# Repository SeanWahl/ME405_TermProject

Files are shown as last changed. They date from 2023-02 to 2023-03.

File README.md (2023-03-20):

# ME 405 Term Project: Nerf Sentry Turret

Group: Mecha15
Sean Wahl, Nathan Dodd, Lewis Kanagy

## Overview

The goal of the Nerf Sentry Turret project is to learn by doing some of the most importnat topics in ME 405. These topics include 
designing systems of modest complexity with both mechanical and electrical components, using control systems to operate mechanical systems, and 
organizing software into discrete modules to call between python files. 

The project entails the consturction and calibration of a thermal sensing target acquisition system that can launch a projectile beyond 
16 feet. The team must use a given thermal camera, STM32 MCU Unit, and a selected Nerf launcher to "duel" an opposing team. The two teams are 
placed 16 feet apart, and upon a "Start" signal, the opposing systems must rotate 180 degrees using mechanical components, gather thermal data through I2C communication,
and use electical components to fire the launcher.

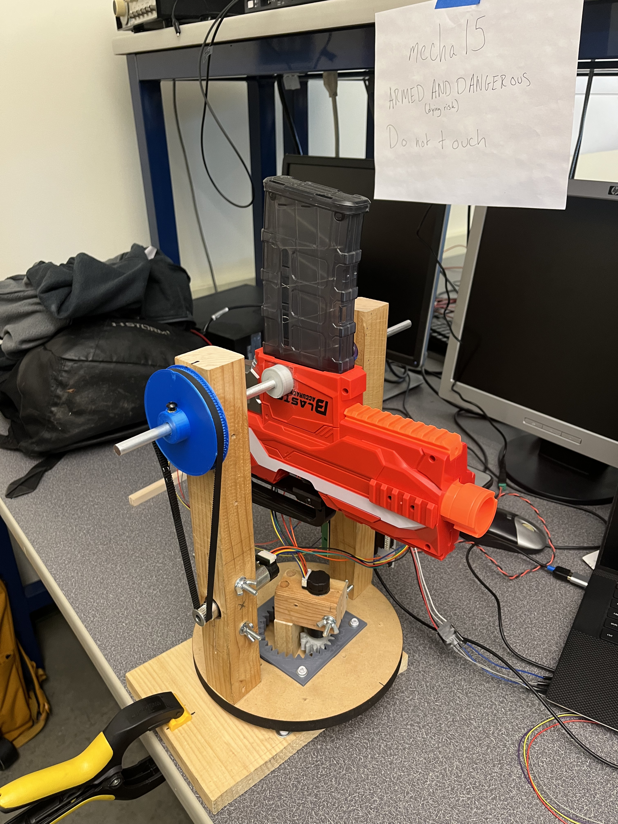
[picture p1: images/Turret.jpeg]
Final Turret


Figure 5.1. Final Nerf Sentry Turret Design

## Mechanical Design

The group began by mechanically designing the spinning base of the system, as seen in Figure 5.2. The system consists of a 3-D printed Internal gear, rotated by another
3-D printed gear head press fit onto the given ME 405 motor shaft. The circular wooden base rotates upon the rectangular base via a purchased, commercially available 
"lazy susan." The motor is mounted using a similar system to the ME 405 motor mounts, with a through hole in a wooden block tightened to hold the motor from the compressive
force applied thorugh the screw/wingnut components. Therefore, as the motor is spun, it rotates the entire circular wooden base which all components rest upon. 

Base Assembly

FIgure 5.2. Base Assembly

The top assembly was constructed the following week, composing of two standing obelisks, two bearings, the mounted shaft, and finally, the nerf gun. The obelisks are screwed
into the circular base, and with one of the obelisks using a similar clamping mechanism as the "yaw" motor to mount the "pitch" motor. The rotating mechanism is controlled by 
the gear-pulley system seen in Figure 5.1. Additionally, through holes are drilled  in the top of each obelisk to allow the alumnium shaft to pass thorugh, with bearings inlayed 
in the wood to house the metal shaft. Finally, the nerf gun is mounted to the shaft via 3-D printed brackets press fit onto the shaft; these brackets have a flat portion, as does the 
shaft, allowing the rotating shaft to rotate the gun as needed.

## Electrical Design

Mounted to the bottom assembly is the given ME 405 STM32 MCU unit, including the proper motor driver board (Figure 5.3). The MCU has wiring to the base motor (yaw) and obelisk 
motor (pitch) to give the system its two degrees of freedom; the intitialization, operation, and control of these motors can be found in the attached source code. The 
nerf gun itself is operated through a "hotwiring" approach, with the its two systems, flywheel and dart push mechanisms, wired to an attached bread board. The board 
contains relays, resistors, and mosfets to apply a set amount of voltage to the gun from the Nucleo GPIO pins. 

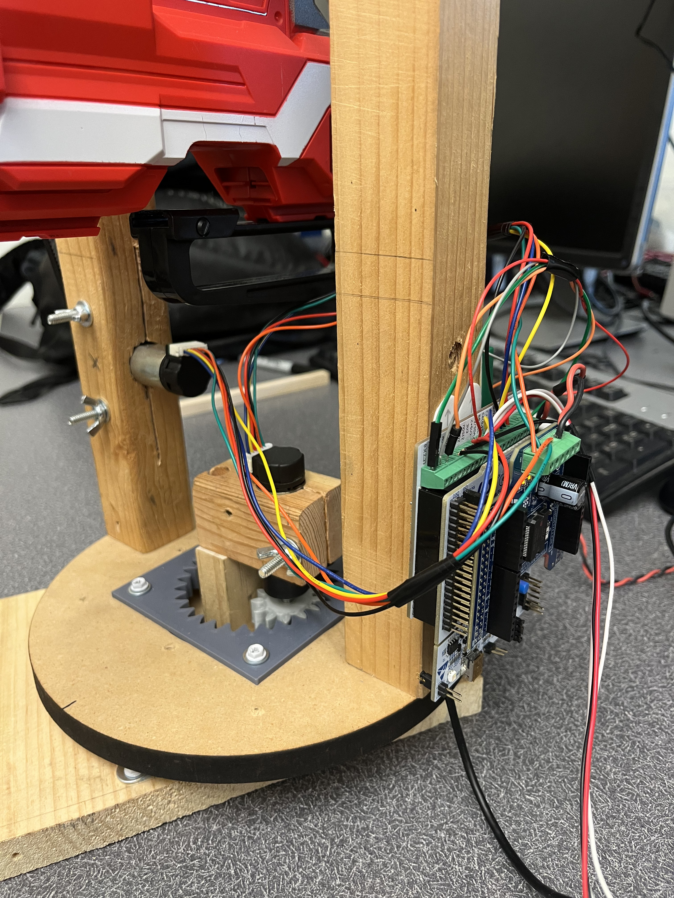
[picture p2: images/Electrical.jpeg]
Electronics


Figure 5.3. Electrical Assembly

## Software Design 

The software used for the project can all be found in the source code folder (src) found in the github page. A general overview of the software design can be better understood by 
looking at the attached State Transition Diagrams found at the bottom of the README file. 

Touching upon the thermal camera tracking algorithim, the camera was placed 8 feet in front of the turret system in order to give the highest image resolution to be analyzed. Within the 
mlx_camera.py file, the data received through the lens was a 24 row x 32 column csv grid of values 0-99, representing the magnitude of heat signature received. The code added to
the given mlx_camera.py analyzed each column upon taking a photo, averaged values in each column, and returned the column index. Given that opponents could only stand up against the table
and not off the sides, the table width was mapped out to the number of columns the camera can place. Assuming that the camera and turret would be placed in the same location every test, 
a unit conversion between (table width/columns) and (yaw position/table width) allowed a set position to be sent to the motor for a given "hottest column." A rough sketch of this can be
found below in Figure 5.4.

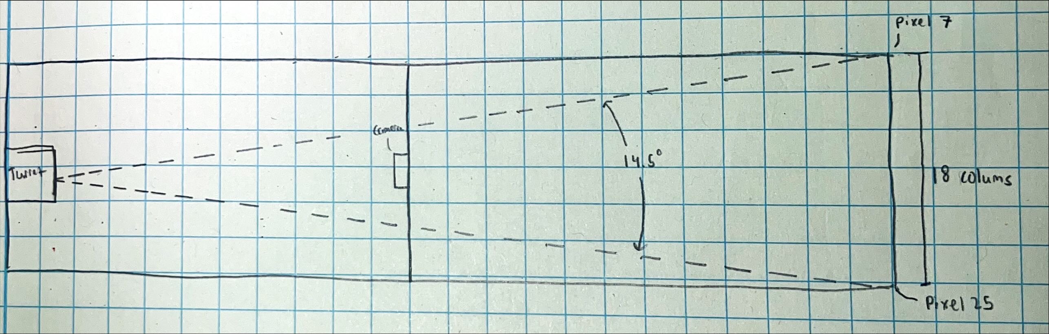
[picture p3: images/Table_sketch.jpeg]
Table Sketch


Figure 5.4. Sketch of table geometry to derive yaw motor setpoint given a "hot column" value.

## Project Results

The system that was designed, manufactured, and tested performed exceedingly well in testing prior to the performance on the dueling day. In nearly every test ran in which the motors
were set to a given setpoint, the thermal camera was allowed 1 second to record a picture, and the opponent did not move within the 1 second, the sentry could accurately move the yaw
motor and "track" a given heat signature and fire at will. When facing opponents in the testing phase, the turret would hit the opponent first before the opponent would fire, 
allowing the team to gain confidence heading into the dueling day. Come match day, all mechanical and electrical components worked, however in the final critical round, the 
magazine was forgotten to be refilled, leading to a defeat. Although this was difficult to grasp, the team was confident that should the magazine have been loaded, it surely would have
resulted in a hit target and a victory.

After undertaking this project for 3 weeks, the team has learned an outstanding amount about the mechatronics design process; even more so, the group has learned what worked well
and what has not for our specific system. Regarding software design, we originally attempted to configure the cotask.py, task_share.py, and basic_tasks.py files to allow for 
priority based scheduling of tasks. We quickly encountered problems, as this priorty task organization encountered issues when tasks, such as the camera task needing over 1 second
to capture an image, would go over its set period time. Instead, the software design of the main file entailed a much simpler finite state machine, swithcing between two simple states.
Going away from this task-sharing system sooner rather than later would have allowed for more time for the group to finalize designs such as camera placement, 

What worked well mechanically was the relatively small gear ratio for the "yaw" axis. The base plate was able to turn around quickly compared to other groups in the section, primarily
due to the gear ratio of 2.5. When facing groups with many more teeth on their internal gears, they were mechanically limited in the speed at which they could rotate. 
3-D printing the gears allowed for larger design control over this element; larger gear teeth worked well, as they were easier to mesh than the much smaller, 16 teeth gears supplied
in class.

Should further testing and design take place on this specific assembly, a useful addition would be a concrete electrical wiring setup. Given the team was still conducting basic testing
upon the dueling date, a clear, robust wiring setup could not be formed. Further research could also be done to use a different MCU running C/C++ code, as this seemed succesful for 
other groups in allowing for up to 60 captures / second; the software/hardware used permitted for roughly 1 capture/second. Further research could prove a useful project for one
interested in any robotics, mechanical design, or thermal camera applications.

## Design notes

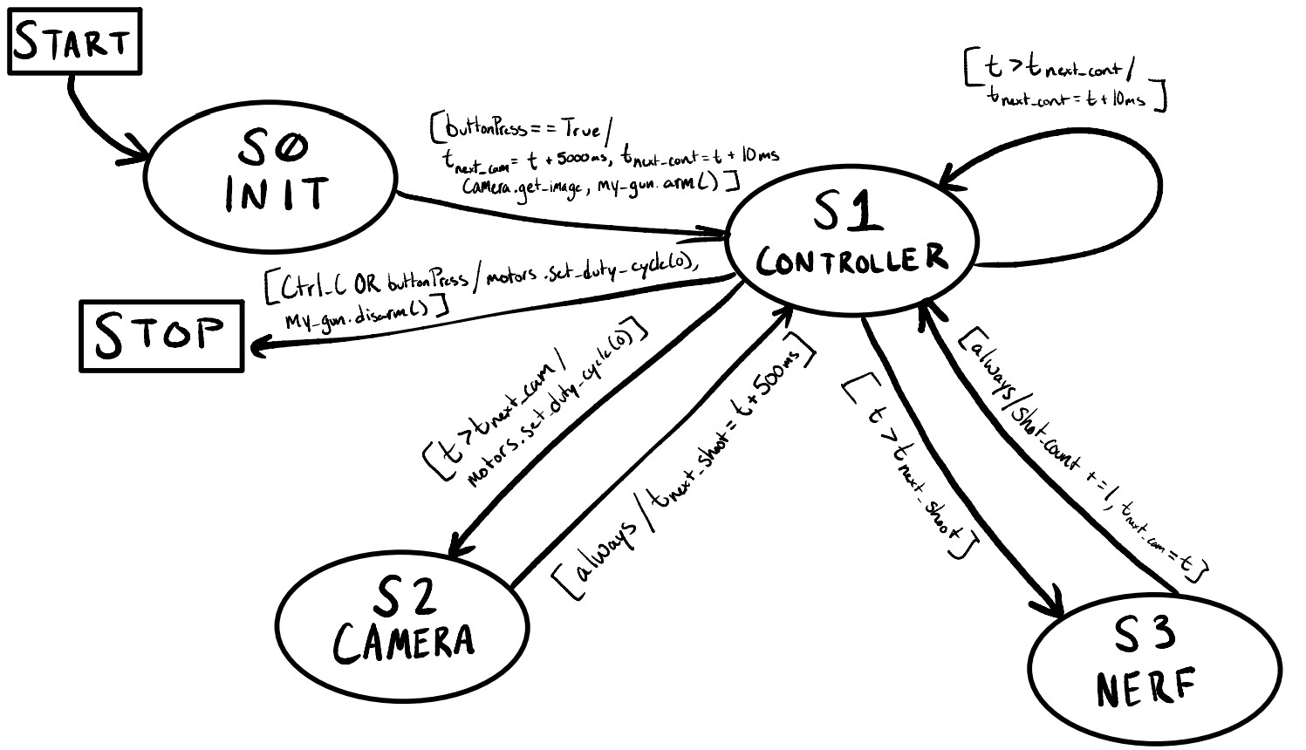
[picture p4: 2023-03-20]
docs/STD.jpg

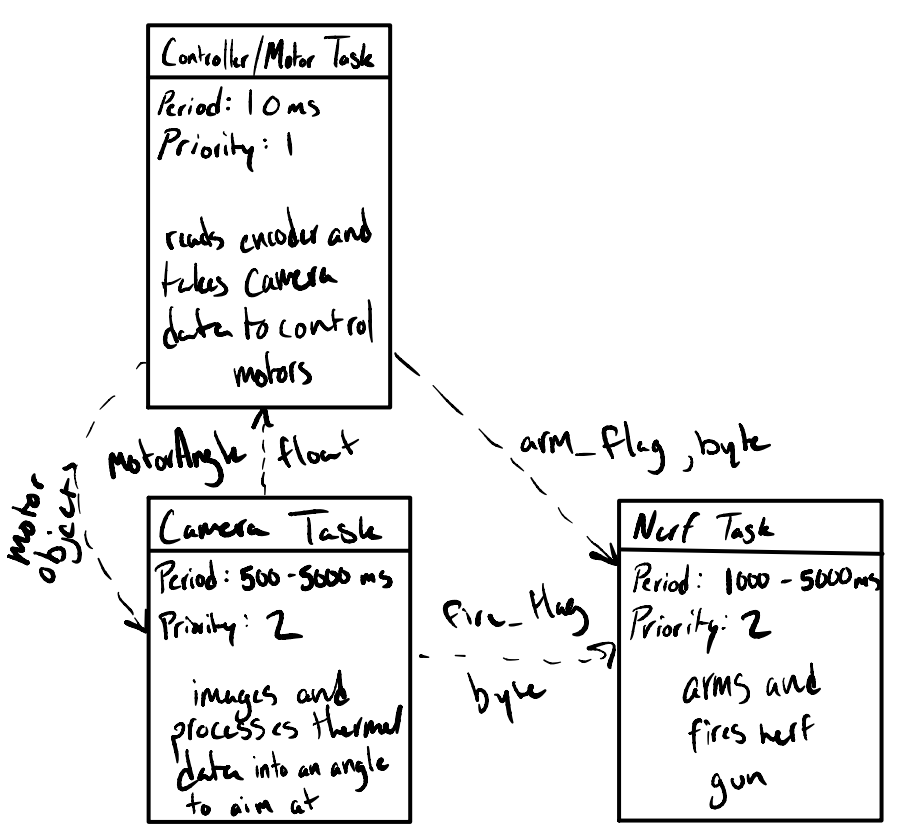
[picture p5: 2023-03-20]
docs/psuedoTasks.png

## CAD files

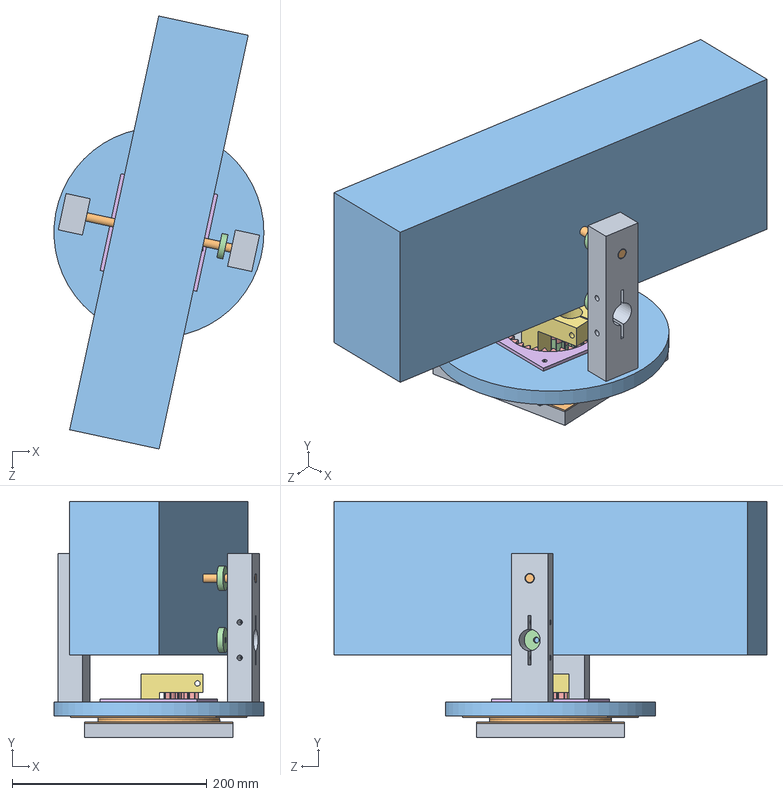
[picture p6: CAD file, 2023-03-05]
CAD/TermProjectCAD.SLDASM
215.4 x 242.3 x 444.4 mm
Bottom Wooden Base^TermProjectCAD
Turn Table Half^TermProjectCAD x 2
Top Wooden Base^TermProjectCAD
spur gear_ai
internal spur gear_ai
Internal Gear Inlay^TermProjectCAD
Motor Mount 1^TermProjectCAD
instrument ball bearing_ai x 2
Wood Obelisks^TermProjectCAD
shaft^TermProjectCAD
nerf gun^TermProjectCAD
Pulley^TermProjectCAD x 2

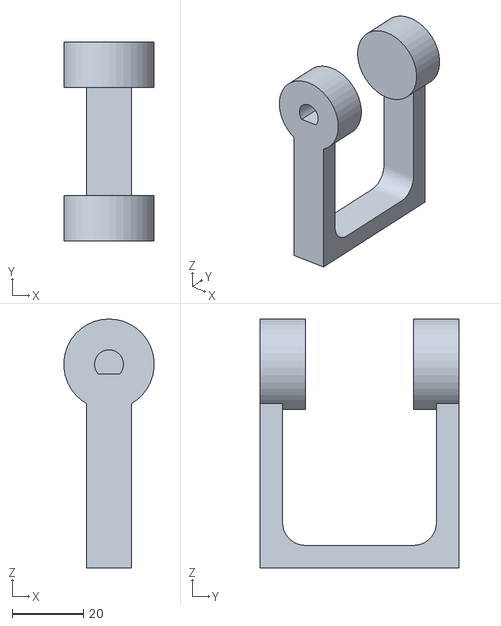
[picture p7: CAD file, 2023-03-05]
CAD/3gunShaftMount.STL
25.3 x 55.8 x 69.8

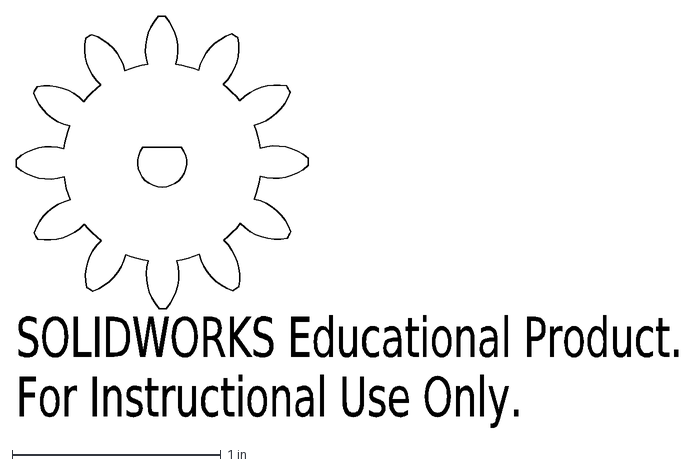
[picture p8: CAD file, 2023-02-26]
CAD/TermProjectCADSmallGear.DXF
SOLIDWORKS Educational Product.
For Instructional Use Only.

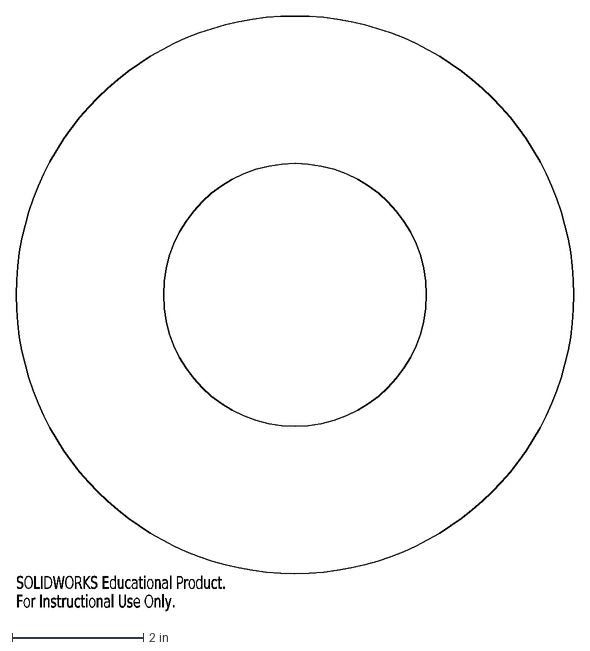
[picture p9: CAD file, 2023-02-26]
CAD/TermProjectTopBase.DXF
SOLIDWORKS Educational Product.
For Instructional Use Only.

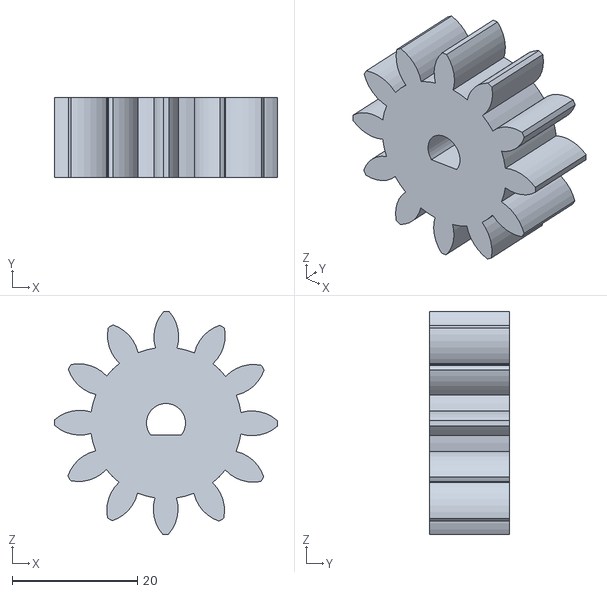
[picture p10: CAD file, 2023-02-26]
CAD/small gear.STL
35.6 x 12.7 x 35.6

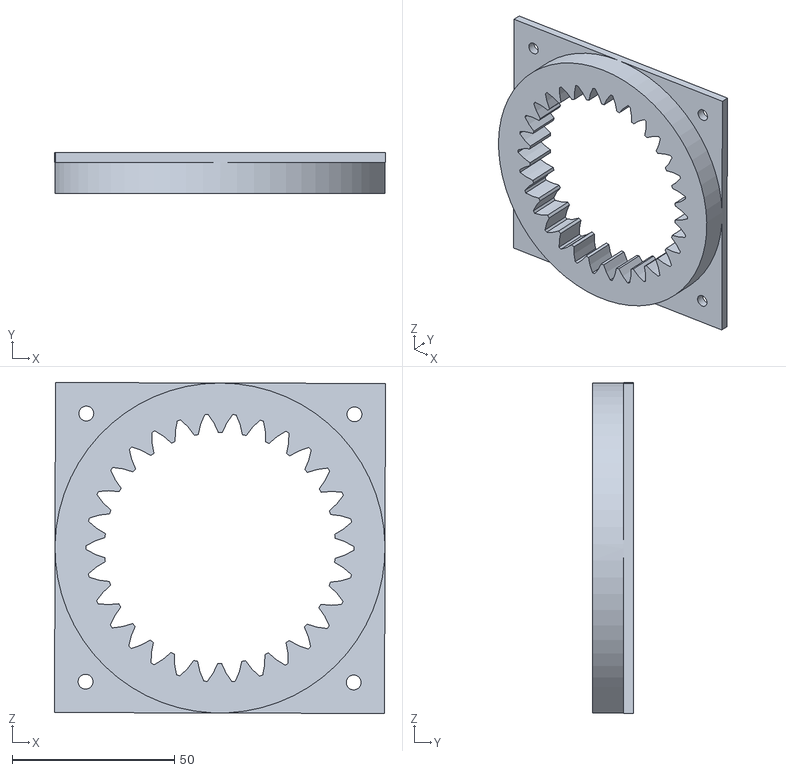
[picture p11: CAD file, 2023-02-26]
CAD/inlay gear.STL
101.9 x 12.7 x 101.9

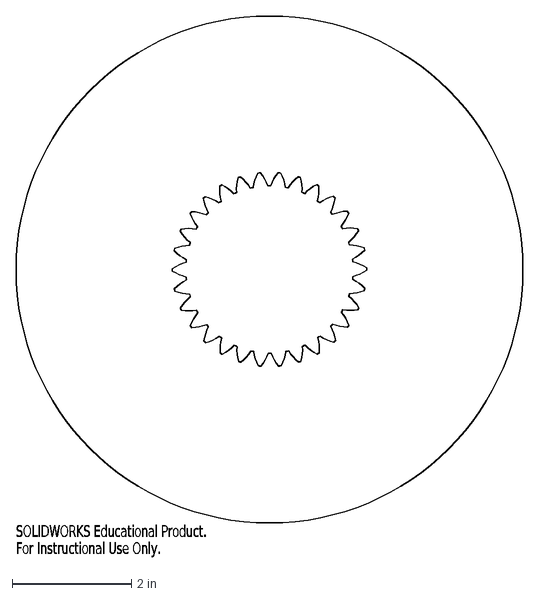
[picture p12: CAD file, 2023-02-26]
CAD/TermProjectCADTopBaseGeared.DXF
SOLIDWORKS Educational Product.
For Instructional Use Only.

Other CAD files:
CAD/gunShaftMount2.STL
CAD/gunShaftMount.SLDPRT
CAD/gunShaftMount.STL

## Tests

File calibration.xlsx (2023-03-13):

col | ang [rad]
24 | 131.28
23 | 130.553
22 | 130.04
20 | 129.468
18 | 128.13
16 | 126.946
15 | 126.21
14 | 126.118
14 | 125.7
12 | 124.946
11 | 124.437
11 | 123.694
10 | 123.197
9 | 122.528
7 | 121.93
1 | 116.76
30 | 133.792

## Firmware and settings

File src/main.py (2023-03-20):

"""!@file   main.py
@brief      Controls the nerf turret.
@details    Contains all necessary code to be able to use the nerf turret. Please
            see the main page for formal task and state diagrams. Essentially,
            this program sets up all necessary objects and then waits for a 
            user indication to start. Upon a button press or the user entering "s",
            the program will start.
            
            Once started, the program takes a picture of the opposite side of the
            table. With this data, it calculates where the opponent is, and converts
            this into a motor angle. The program then continuously controls the motor
            to go to this angle. Upon 5 seconds (when the opponent is no longer
            able to move) the turret takes another picture and adjusts to this position.
            After 0.5s of adjusting, the gun shoots and then takes another picture.
            This process of taking a picture, calculating an angle, adjusting, and
            shooting continues indefinitely. When a shot count maximum is reached,
            the gun will no longer shoot but will still adjust to point at the
            opponent.
            
            At any point, the user can Ctrl-C or press the blue button again to
            exit the program.
@author     Nathan Dodd
@author     Lewis Kanagy
@author     Sean Wahl
@date       March 20, 2023
"""

# Import necessary modules.
import pyb
import math
from nerf import Nerf
from controller import CLController
from motor_driver import MotorDriver
from encoder_reader import encoder
from machine import Pin, I2C
from mlx_cam import MLX_Cam

from time import ticks_ms, ticks_add, ticks_diff

def onButtonPress(IRQ_src):
    """!@brief          Detects interrupt request through blue button press.
        @details        When the button is pressed, this function will set
                        a variable as true, indicating that the button has been
                        pressed and allowing the program to enact on the button
                        press elsewhere.
        @param IRQ_src  Interrupt service request notation. 
    """
    global buttonPressed
    ## Indicates whether or not the blue button has recently been pressed.
    buttonPressed = True

if __name__ == "__main__":
    # The main script of the program. Will set up all necessary objects and then
    # act on states as programmed. Takes care of motor reading/control, camera
    # images, and nerf gun shooting.
    
    ## Serial port object for detecting the user's keyboard inputs, such as "s".
    serport = pyb.USB_VCP()
    
    ## Button interrupt set up for the Nucleo's blue button, attached to pin C13.
    ButtonInt = pyb.ExtInt(pyb.Pin(pyb.Pin.board.PC13), mode=pyb.ExtInt.IRQ_FALLING, pull=pyb.Pin.PULL_NONE, callback=onButtonPress)
    
    # Set up base motor, encoder, and controller objects
    ## Base's motor to move about the yaw axis, turning left and right.
    my_motor_yaw = MotorDriver(pyb.Pin.board.PA10, pyb.Pin.board.PB4, pyb.Pin.board.PB5, 3)
    ## Base motor's encoder.
    my_encoder_yaw = encoder(pyb.Pin.board.PB6, pyb.Pin.board.PB7, 4)
    # Zero the base motor's encoder.
    my_encoder_yaw.zero()
    ## Base motor's closed loop controller.
    my_controller_yaw = CLController(60, .1, math.pi*16*2.5, 0)
    
    # Set up pitch motor, encoder, and controller objects
    ## Pitch axis's motor to point the gun up and down.
    my_motor_pitch = MotorDriver(pyb.Pin.board.PC1, pyb.Pin.board.PA0, pyb.Pin.board.PA1, 5)
    ## Pitch motor's encoder.
    my_encoder_pitch = encoder(pyb.Pin.board.PC6, pyb.Pin.board.PC7, 8)
    # Zero the pitch motor's encoder.
    my_encoder_pitch.zero()
    ## Pitch motor's closed loop controller.
    my_controller_pitch = CLController(30, .1, 8, 0)
    
    ## Nerf gun object for arming and shooting.
    my_gun = Nerf(Pin.board.PB3, Pin.board.PC4)
    
    # Set up dummy periods for the first run of the tasks.
    ## Period for the controller task in ms.
    cont_per = 10
    ## Initial period for the camera task in ms.
    cam_per  = 5500
    ## Inital period for the nerf gun task in ms.
    shoot_per = 4500
    
    try:
        from pyb import info

    # Oops, it's not an STM32; assume generic machine.I2C for ESP32 and others
    except ImportError:
        # For ESP32 38-pin cheapo board from NodeMCU, KeeYees, etc.
        i2c_bus = I2C(1, scl=Pin(22), sda=Pin(21))

    # OK, we do have an STM32, so just use the default pin assignments for I2C1
    else:
        i2c_bus = I2C(1)

    # Select MLX90640 camera I2C address, normally 0x33, and check the bus
    ## MLX90640's I2C address.
    i2c_address = 0x33
    _scanhex = [f"0x{addr:X}" for addr in i2c_bus.scan()]
    print(f"I2C Scan: {_scanhex}")
    
    # Create the camera object and set it up in default mode
    ## The camera object for the MLX90640.
    camera = MLX_Cam(i2c_bus)
    
    # Overall states for this general file. Psuedo states are present though not
    # explicitly called out. Please see the main page.
    ## The state in which user input is waited on to start the control algorithm.
    s0 = 0
    ## The state in which the camera, controller, and nerf gun psuedotasks are run
    #  after user input has been received.
    s1 = 1
    ## The current overall state of the program.
    state = s0
    
    ## Indicates whether or not the blue button has recently been pressed.
    buttonPressed = False
    
    ## How many times the gun has been shot.
    shot_count = 0
    
    print('Press s or the blue button to start.')
    
    while True:
    
        if state == s0:
            # Wait for user input, either a button press or an "s" to start.
            
            # Button press logic.
            if buttonPressed:
                # Reset the button press boolean.
                buttonPressed = False
                
                # Arm the gun.
                my_gun.arm()
                # Zero both encoders.
                my_encoder_yaw.zero()
                my_encoder_pitch.zero()
                ## The time at which the user has started the program, upon
                #  a button press or "s" input.
                t_init = ticks_ms()
                # Go to the pseudotask running state.
                state = s1
                ## The camera's image data.
                image = camera.get_image()
                ## The hottest column of the camera's image.
                column = camera.get_hot_column(image)
                ## The angle at which the yaw motor should turn to in order to
                #  aim at the target.
                motorAngle = .5613 * column + 117.89
                
                # Set the next time for the pseudotasks to run. Note, for the
                # nerf gun this is an arbitrary placeholder time that is just
                # greater than 6 seconds.
                ## The time directly after taking the picture.
                t_rn = ticks_ms()
                ## The time at which the controller task should run again.
                t_next_cont  = ticks_add(t_rn, cont_per)
                ## The time at which the camera task should run again.
                t_next_cam   = ticks_add(t_init, cam_per)
                ## The time at which the nerf gun task should run again.
                t_next_shoot = ticks_add(t_rn, 10_000)
            
            # Check the serial port for an "s" input.
            elif serport.any():
                ## Character data from user's keyboard inputs.
                charIn = serport.read(1).decode()
        
                # Start program if the input is "s".
                if charIn in {'s','S'}:
                    # Arm the gun.
                    my_gun.arm()
                    # Zero both encoders.
                    my_encoder_yaw.zero()
                    my_encoder_pitch.zero()
                    # Set the initial time.
                    t_init = ticks_ms()
                    # Go to the pseudotask running state.
                    state = s1
                    # Take a picture.
                    image = camera.get_image()
                    # Get the hottest column.
                    column = camera.get_hot_column(image)
                    # Calculate where the yaw motor should turn to.
                    motorAngle = .5613 * column + 117.89
                    
                    # Set the next time for the pseudotasks to run. Note, for the
                    # nerf gun this is an arbitrary placeholder time that is just
                    # greater than 6 seconds.
                    t_rn = ticks_ms()
                    t_next_cont  = ticks_add(t_rn, cont_per)
                    t_next_cam   = ticks_add(t_init, cam_per)
                    t_next_shoot = ticks_add(t_rn, 10_000)
                
        if state == s1:
            try:
                
                # If the button is pressed, stop running.
                if buttonPressed:
                    # Reset the button press boolean variable.
                    buttonPressed = False
                    # Disable the motors.
                    my_motor_pitch.set_duty_cycle(0)
                    my_motor_yaw.set_duty_cycle(0)
                    # Disarm the gun.
                    my_gun.disarm()
                    print('Exiting')
                    # Quit the program.
                    break
                
                # Camera pseudotask.
                if ticks_diff(ticks_ms(), t_next_cam) >=0:

                    # Disabling the motors before taking the picture for ~500ms
                    # to avoid issues.
                    my_motor_yaw.set_duty_cycle(0)
                    my_motor_pitch.set_duty_cycle(0)
                    
                    # Get image and calculate yaw motor angle.
                    image = camera.get_image()
                    print('Click')
                    column = camera.get_hot_column(image)
                    motorAngle = .5613 * column + 117.89
                    
                    # Stall next camera shot an arbitrary amount.
                    t_next_cam = ticks_add(ticks_ms(), cam_per)
                    
                    # Tell gun to shoot in .5 seconds to allow for motor adjustment.
                    t_next_shoot = ticks_add(ticks_ms(), 500)
                    
                # Nerf gun psuedotask.
                elif ticks_diff(ticks_ms(), t_next_shoot) >= 0:
                    
                    # Shoot the nerf gun if less than 2 shots have been taken.
                    if shot_count < 2:
                        # Shoot the nerf gun.
                        my_gun.shoot()
                        # Increment the shot counter.
                        shot_count += 1
                        
                    # If the gun has been shot twice, disarm the gun.
                    elif shot_count == 2:
                        # Disarm the nerf gun.
                        my_gun.disarm()
                        # Increment the counter so that this block only runs once.
                        shot_count += 1
                    
                    # Tell camera to take another picture now.
                    t_next_cam = ticks_ms()
                    
                 
                # Controller psuedotask.
                elif ticks_diff(ticks_ms(), t_next_cont) >= 0:
                    # Tell the task to run again in 10ms if possible.
                    t_next_cont = ticks_add(ticks_ms(), cont_per)
                    
                    # Set yaw motor controls.
                    # Update the yaw motor.
                    my_encoder_yaw.read_encoder()
                    # Update the controller's positional set point.
                    my_controller_yaw.set_Pos(motorAngle)
                    ## The duty cycle applied to the yaw motor, calculated through
                    #  a closed loop control law.
                    actuation_yaw = my_controller_yaw.run(my_encoder_yaw.read_Posrad(), my_encoder_yaw.read_Velrad())
                    # Apply the actuation value to the yaw motor.
                    my_motor_yaw.set_duty_cycle(actuation_yaw)
                    
                    # Set pitch motor controls. Note, the pitch motor is kept at
                    # constant angle.
                    # Update the pitch motor.
                    my_encoder_pitch.read_encoder()
                    ## The duty cycle applied to the pitch motor, calculated through
                    #  a closed loop control law.
                    actuation_pitch = my_controller_pitch.run(my_encoder_pitch.read_Posrad(), my_encoder_pitch.read_Velrad())
                    # Apply the actuation value to the pitch motor.
                    my_motor_pitch.set_duty_cycle(actuation_pitch)
                
            except KeyboardInterrupt:
                # If Ctrl+C is entered, disable the motors.
                my_motor_pitch.set_duty_cycle(0)
                my_motor_yaw.set_duty_cycle(0)
                # Disarm the gun.
                my_gun.disarm()
                print('Exiting')
                # Exit the program.
                break

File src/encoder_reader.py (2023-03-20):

"""!@file encoder_reader.py
@brief      Documents the encoder class for ME 405.
@details    Contains the "encoder" class that can be used to set up encoder objects
            that will be used in future labs. Encoders are able to sense positional
            changes, allowing for angle control or rotational speed calculations.
@author     Nathan Dodd
@author     Lewis Kanagy
@author     Sean Wahl
@date       January 31, 2023
"""

# Import necessary modules.
import time, pyb, math

class encoder:
    """!@brief      Implements an encoder class to be used in lab.
       @details     An encoder class compatible with the encoders in the ME 405 lab
                    kits. Allows for functions such as reading and zeroing.
    """
    
    def __init__(self, pin1, pin2, timer):
        """!@brief          Initializes an encoder object.
            @details        Using pin objects as inputs, is able to create an encoder
                            capable of sensing positional changes through the use of
                            the timer's counting ability.
            @param pin1     Pin object connected to encoder channel A. 
            @param pin2     Pin object connected to encoder channel B.
            @param timer    Timer channel (has to be compatible with pins 1 and 2)
        """
        ## Pin object representing the connection to channel A of the encoder.
        self.pin1 = pyb.Pin(pin1, pyb.Pin.OUT_PP)
        ## Pin object representing the connection to channel B of the encoder.
        self.pin2 = pyb.Pin(pin2, pyb.Pin.OUT_PP)
        ## Timer object used for adding the encoder's positional changes.
        self.timer = pyb.Timer (timer, period = 0xFFFF, prescaler = 0)
        ## Channel associated with channel A of the encoder, will count in one direction.
        self.ch1 = self.timer.channel(1, pyb.Timer.ENC_AB, pin=self.pin1)
        ## Channel associated with channel B of the encoder, will count in the opposite direction.
        self.ch2 = self.timer.channel(2, pyb.Timer.ENC_AB, pin=self.pin2)
        ## Overall position of the encoder in ticks.
        self.count = 0
        ## The previous timer count value.
        self.prev = 0
        
        # Time and position lists for velocity calculation.
        self._timelist = [0]*5
        self._poslist = [0]*5
        
    def read_encoder(self):
        """!@brief          Retrieves the overall position of the encoder.
            @return         The total position of the encoder in ticks.
        """
        ## The current timer count value.
        self.current = self.timer.counter()
        ## The change in timer count value from the last update.
        self.delta = self.current-self.prev
        # Check for overflow/underflow
        if abs(self.delta) > (0xFFFF+1)/2:
            if self.delta > 0:
                self.count -= self.delta - 0xFFFF
            else:
                self.count -= self.delta + 0xFFFF
        else:
            self.count -= self.delta
        
        # Append the position and time lists as necessary.
        self._poslist.pop(0)
        self._poslist.append(self.count)
        self._timelist.pop(0)
        self._timelist.append(time.ticks_us())
        
        self.prev = self.current
        return self.count
        
    def read_Posrad(self):
        """!@brief          Retrieves the overall position of the encoder in radians.
            @return         The total position of the encoder in radians.
        """
        return self.read_encoder()*2*math.pi/(256*4)
    
    def read_omega(self):
        """!@brief          Retrieves the rotational velocity of the encoder.
            @return         The rotational velocity of the encoder in ticks/second.
        """
        omega = (self._poslist[0]-self._poslist[4])/(time.ticks_diff(self._timelist[0], self._timelist[4])/1000000)
        return omega
    
    def read_Velrad(self):
        """!@brief		Retrieves the rotational velocity of the encoder in radians/s.
            @return     The rotational velocity of the encoder in r/s.
        """
        return self.read_omega()*2*math.pi/(256*4)
    
    def zero(self):
        """!@brief          Sets the encoder's overall position value back to zero.
        """
        self.count = 0
        self.prev = self.timer.counter()
        
if __name__ == "__main__":
    #Set up an encoder, have it read 9 times and zero on the tenth.
    #my_encoder = encoder(pyb.Pin.board.PB6, pyb.Pin.board.PB7, 4)
    my_encoder = encoder(pyb.Pin.board.PC6, pyb.Pin.board.PC7, 8)
    my_encoder.zero()
    while True:
        for n in range(100):
            my_encoder.read_encoder()
        if n == 99:
            print(f'pos:{my_encoder.read_Posrad()}, vel:{my_encoder.read_Velrad()}')
        time.sleep(0.010)

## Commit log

2023-02-26 build day 1
    [TermProjectCAD.SLDASM, TermProjectCADSmallGear.DXF, TermProjectCADTopBaseGeared.DXF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]
2023-02-28 Thermal Camera Code
2023-02-28 CAD updates
    [TermProjectCAD.SLDASM]
2023-03-04 shaft to gun fixture
    [gunShaftMount.SLDPRT, gunShaftMount.STL]
2023-03-05 updates on CAD for gun shaft mount
    [3gunShaftMount.STL, TermProjectCAD.SLDASM, gunShaftMount.SLDPRT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]
